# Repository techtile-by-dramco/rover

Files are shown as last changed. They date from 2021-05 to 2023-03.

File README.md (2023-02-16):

## Documentation

- The `rpi` folder contains the Python scripts to collect the sensor readings from the sensor-reader (`Sensorcombiner.py`) and driving the motors (with the rotary encoderers).
- The `scissor-lift` folder contains the files to talk the the scissor lift microcontrollers (Adruino Uno + custom-made shield) through Python. More information is included in the [docs](https://jarnevanmulders.github.io/scissor-lift-docs/).
- The `sensor-reader`folder contains the source files for the microcontroller to read-out all sensors on the rover. This microcontroller is read-out by the RPI on the rover (as dicussed above).

## System Architecture

Architecture

## System Description
To speed-up measurements, reduce labor-intensive tasks and mitigate human-errors, we have designed a rover
to perform automated 3D sampling inside the testbed. The rover consists of a baseplate, hosting the processing
unit and batteries, and a scissor lift to move the measurement equipment to the required height.

### Baseplate 
The baseplate contains a Raspberry Pi. A 16 cells battery pack, in a 4S4P configuration, powers the system. 
The battery voltage ranges from 10 V to 16.2 V depending on the charge state. The battery back, based on Lithium Cobalt Oxide (LCO) technology,
has a capacity of 170Wh and can handle up to 480W peak power. Besides powering the rover, the battery pack
provides power to the peripherals and measurement equipment in order to conduct the experiments. When
the battery is low, the rover is able to navigate to its charging station, recharge and resume the measurements.

### Navigation
Marvelmind indoor RTLS is used as a positioning system. It has a precision of 2 cm.
Ultrasonic beacons are used to acquire the position of the mobile beacon (mounted on the baseplate). Four
beacons are fixed in the Techtile infrastructure. The position is determined by trilateration. To filter out
outliers, we make use of a Kalman filter. The recursive algorithm uses consecutive inputs to estimate the
current state. Based on the uncertainties of the inputs and the uncertainties of the previous estimates, the
current state is approximated. Besides localization, the rover features obstacle detection to mitigate crashing into objects in the room. 
Ultrasonic sensors mounted on the sides of the rover’s baseplate are used and have
a resolution of 3 mm and a range of 2 cm to 400 cm.

### Scissor lift.
The baseplate of the rover can navigate through the room in 2D space. By mounting the scissor
lift on top of the baseplate, the rover is able to measure in 3D space. The lift has a range of 55 cm
to 185 cm. The equipment can be mounted on top of the lift. Power is supplied to the equipment from the
battery pack. The scissor lift can be controlled with AT-commands. The height of the lift is determined by
the VL53L1X Time-of-Flight (ToF) sensor using a 940 nm invisible Class 1 laser. An advertised accuracy and
ranging error of ± 20 mm in both ambient light and dark light conditions.

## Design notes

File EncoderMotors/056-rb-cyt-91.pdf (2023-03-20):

## RB-Cyt-91

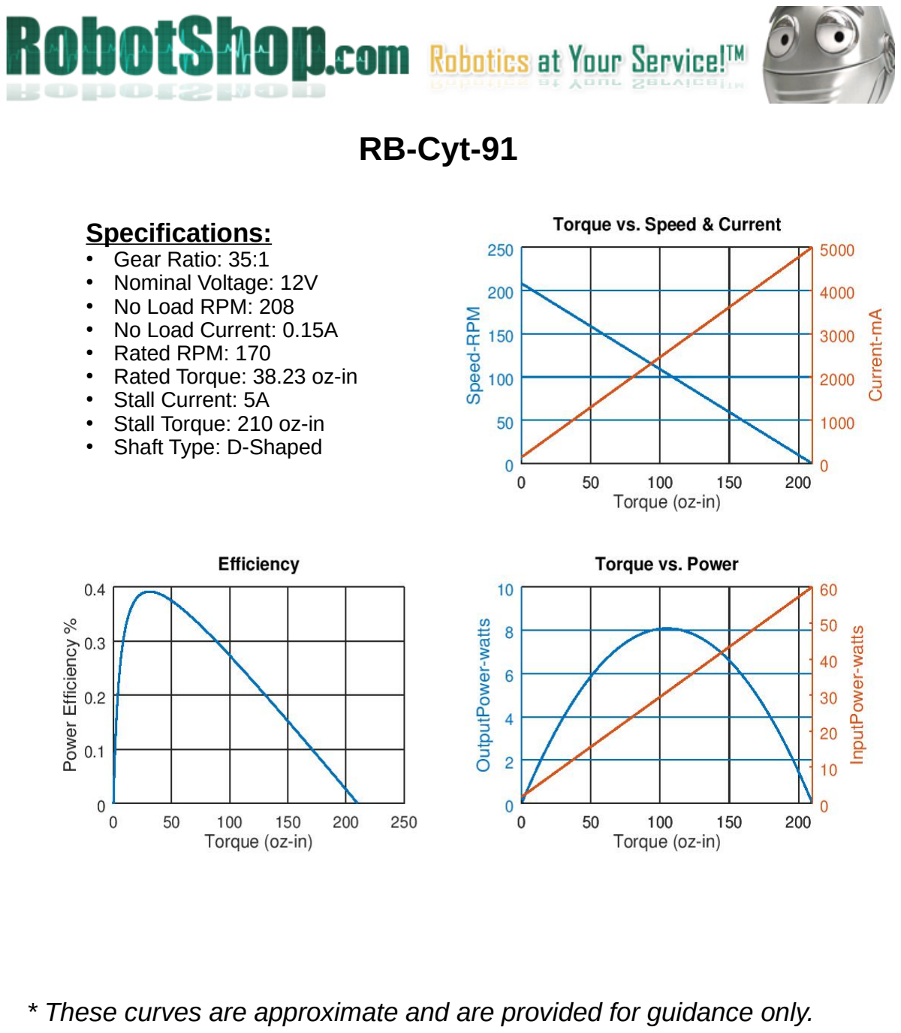
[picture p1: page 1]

* These curves are approximate and are provided for guidance only.

### Specifications:

- Gear Ratio: 35:1
- Nominal Voltage: 12V
- No Load RPM: 208
- No Load Current: 0.15A
- Rated RPM: 170
- Rated Torque: 38.23 oz-in
- Stall Current: 5A
- Stall Torque: 210 oz-in
- Shaft Type: D-Shaped

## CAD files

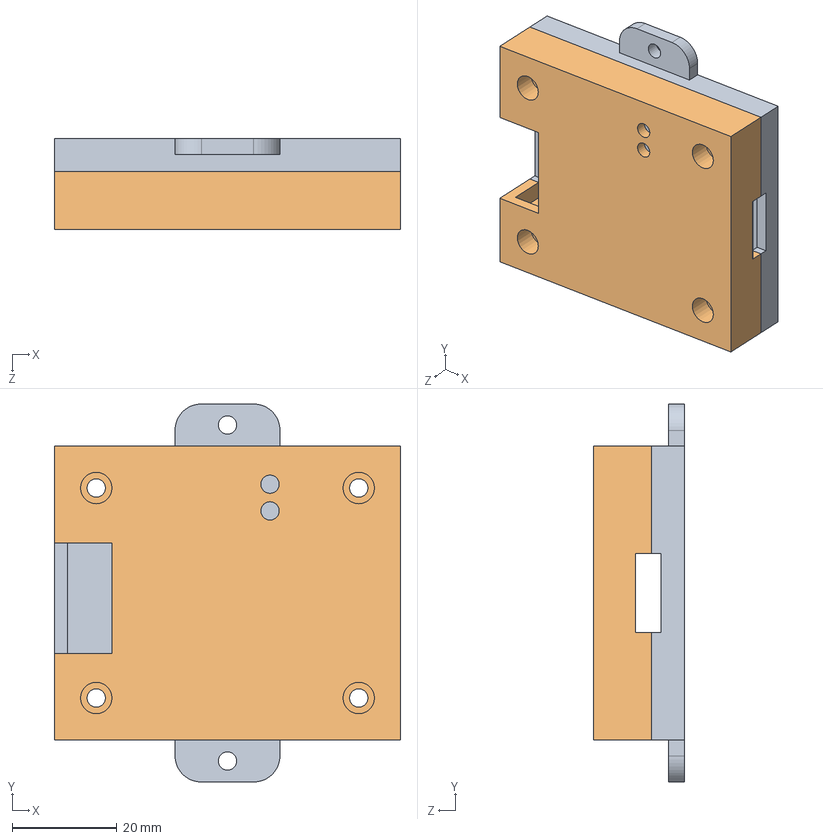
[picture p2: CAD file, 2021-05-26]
scissor-lift/drawings/Assembly/LEDstripControllerBox.SLDASM
66.0 x 72.0 x 17.3 mm
LEDstripController_Bottom
LEDstripController_Top

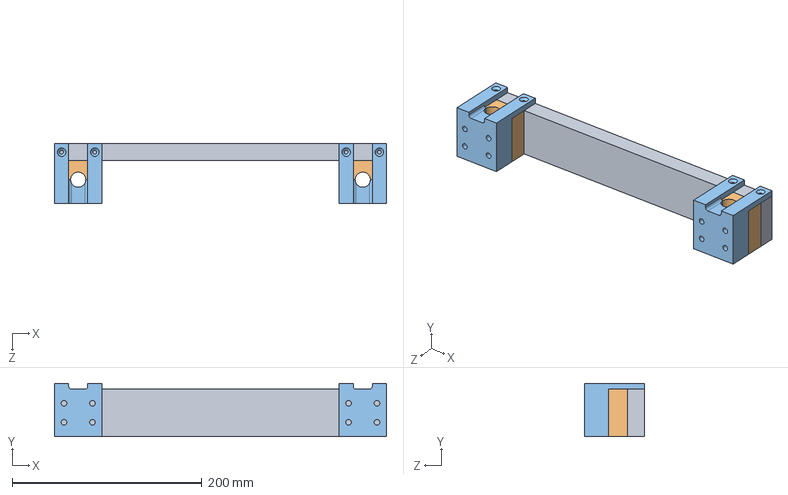
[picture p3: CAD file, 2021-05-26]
scissor-lift/drawings/Part-Files/Mounting_Fixed_Point_V2/Assembly_V2.SLDASM
350.0 x 56.0 x 63.0 mm
Scisser_Lift_Steel_Rod_Mounting_Part_Top_Fixed_Scissor_Wood
Scisser_Lift_Steel_Rod_Mounting_Part_Top_Fixed_Scissor x 2
Scisser_Lift_Steel_Rod_Mounting_Part x 2

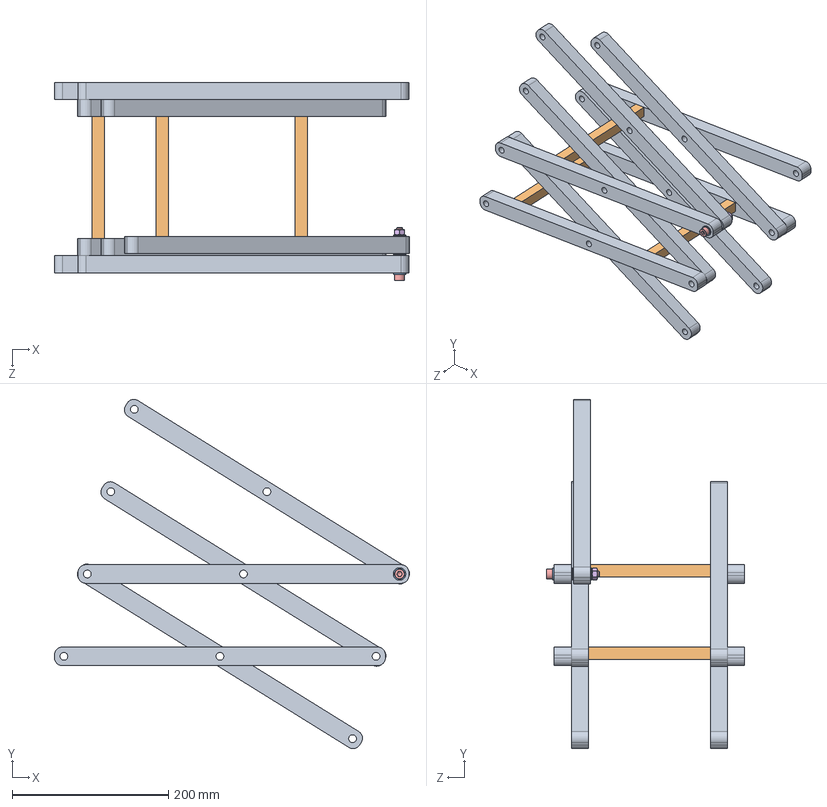
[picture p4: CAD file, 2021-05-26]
scissor-lift/drawings/Part-Files/Assembly.SLDASM
454.8 x 447.5 x 254.1 mm
Scisser_Lift_Main_Bar x 9
Scisser_Lift_Main_Bar_Transversal x 3
Scisser_Lift_Main_M8_Washer x 3
Scisser_Lift_Main_Round_Tube_23mm x 2
socket head cap screw_iso
hex nut style 1 gradeab_iso

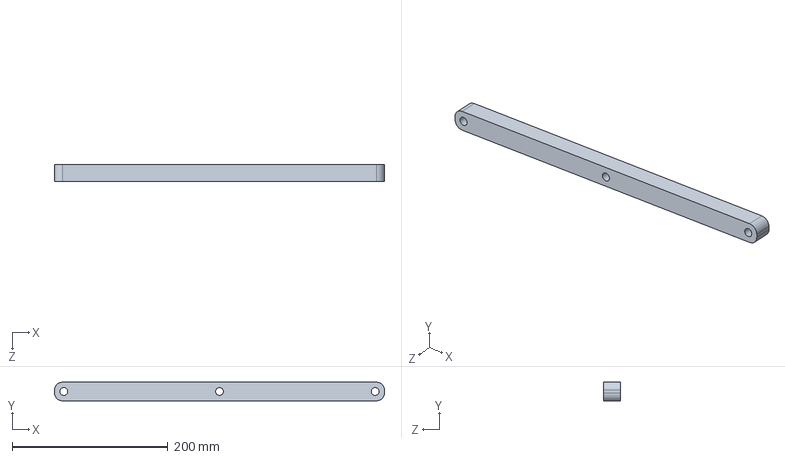
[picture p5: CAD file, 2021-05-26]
scissor-lift/drawings/Part-Files/Scisser_Lift_Main_Bar.SLDPRT
424.0 x 24.0 x 22.0 mm

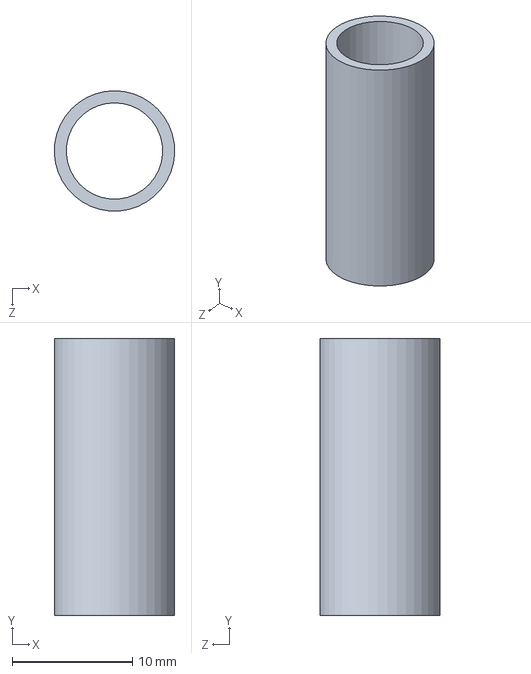
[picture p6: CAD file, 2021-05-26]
scissor-lift/drawings/Part-Files/Scisser_Lift_Main_Round_Tube_23mm.SLDPRT
9.99 x 23.0 x 10.0 mm

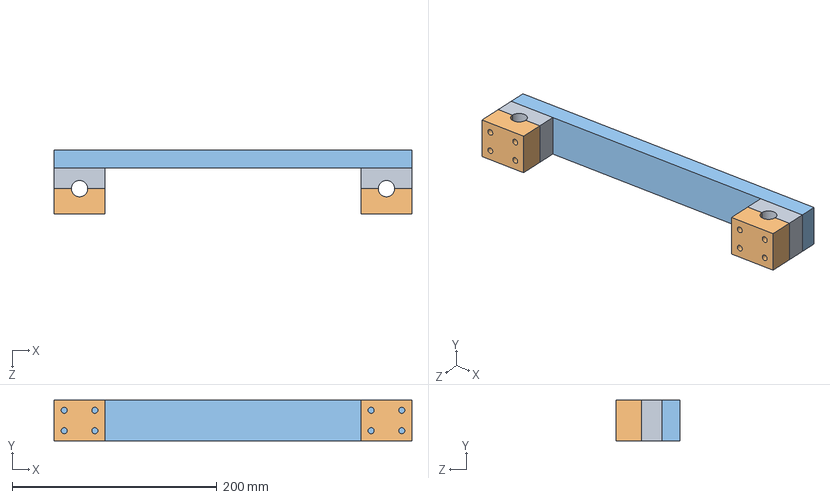
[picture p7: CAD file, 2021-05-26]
scissor-lift/drawings/Part-Files/Steel_Rod_Assembly_Fixed_Scissor.SLDASM
350.0 x 40.0 x 63.0 mm
Scisser_Lift_Steel_Rod_Mounting_Part_Top_Fixed_Scissor x 2
Scisser_Lift_Steel_Rod_Mounting_Part x 2
Scisser_Lift_Steel_Rod_Mounting_Part_Top_Fixed_Scissor_Wood

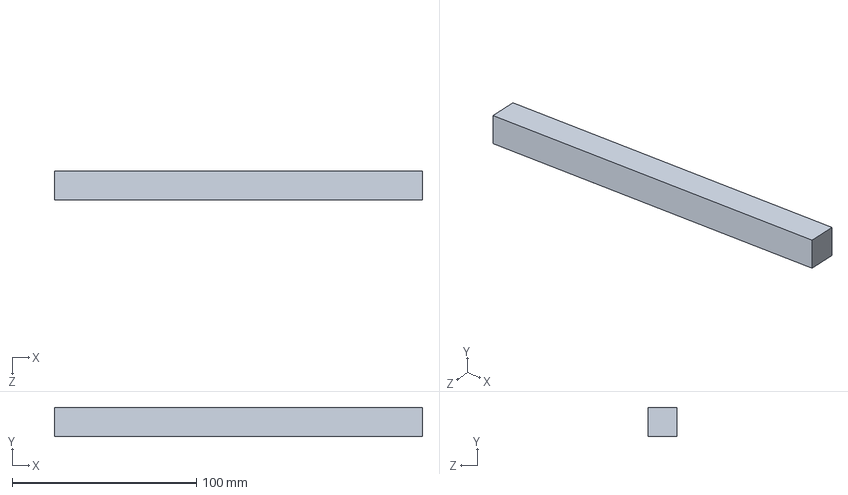
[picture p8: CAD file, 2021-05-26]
scissor-lift/drawings/Part-Files/Scisser_Lift_Main_Bar_Transversal.SLDPRT
200.0 x 16.0 x 16.0 mm

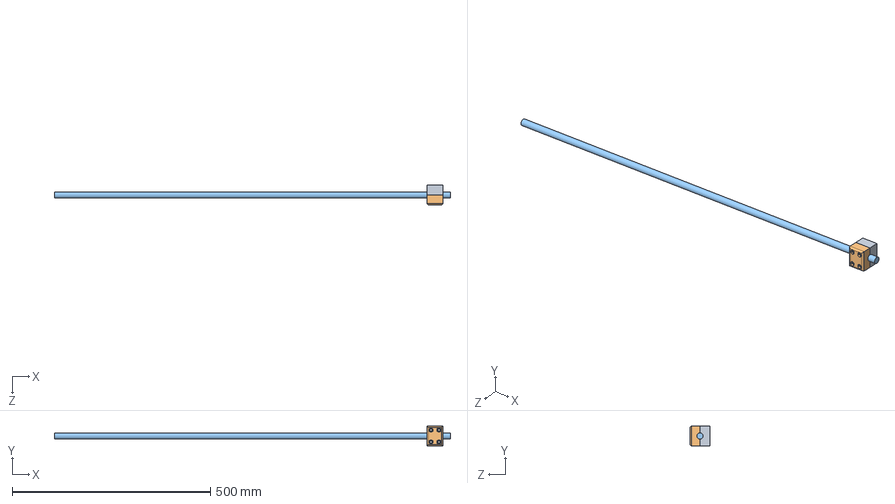
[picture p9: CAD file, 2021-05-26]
scissor-lift/drawings/Part-Files/Steel_Rod_Assembly.SLDASM
1000.0 x 50.0 x 50.0 mm
Scisser_Lift_Steel_Rod_Mounting_Part
Scisser_Lift_Steel_Rod_Mounting_Part_Top
Steel_Rod_16mm

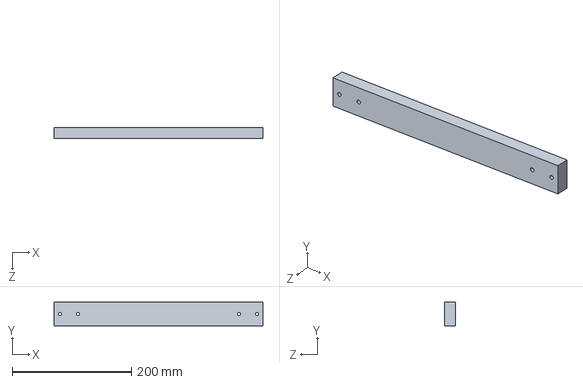
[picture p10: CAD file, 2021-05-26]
scissor-lift/drawings/Part-Files/Scisser_Lift_Steel_Rod_Mounting_Part_Top_Fixed_Scissor_Wood.SLDPRT
350.0 x 40.0 x 18.0 mm

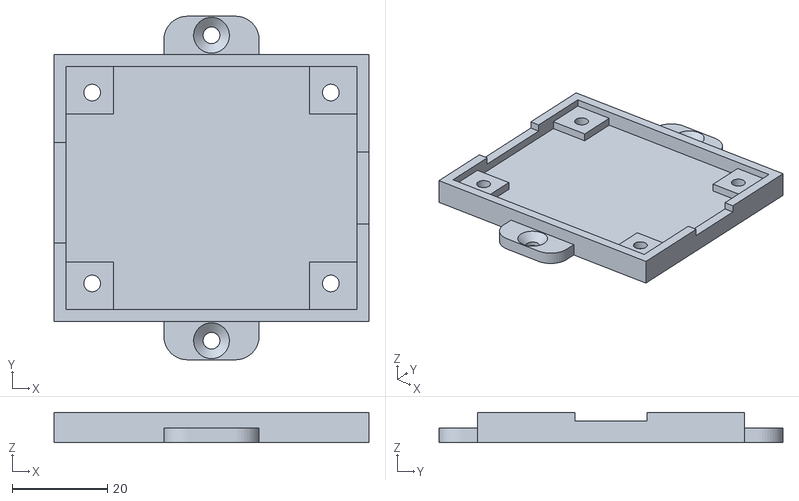
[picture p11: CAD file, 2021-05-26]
scissor-lift/drawings/STL-Files/LEDstripController_Bottom.STL
66.0 x 72.0 x 6.30

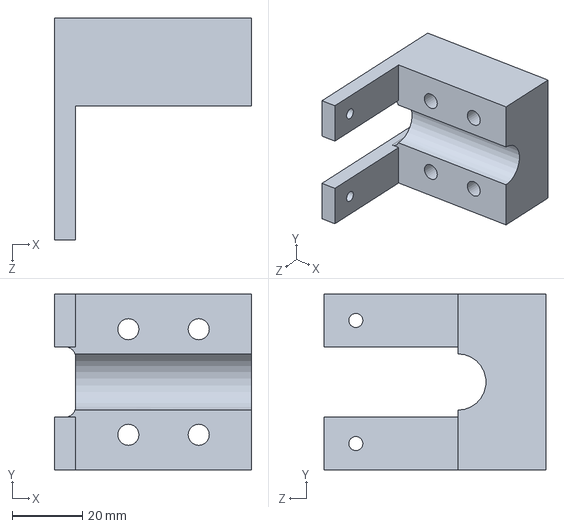
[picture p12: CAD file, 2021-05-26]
scissor-lift/drawings/Part-Files/Mounting_Fixed_Point_V2/Scisser_Lift_Steel_Rod_Mounting_Part.SLDPRT
56.0 x 50.0 x 63.0 mm

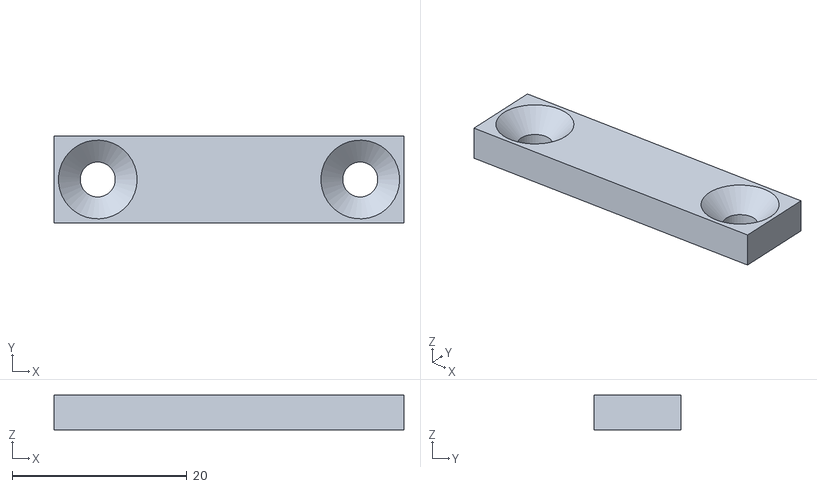
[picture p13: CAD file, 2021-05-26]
scissor-lift/drawings/STL-Files/LEDSTRIP_Mounting.STL
40.0 x 10.0 x 4.00

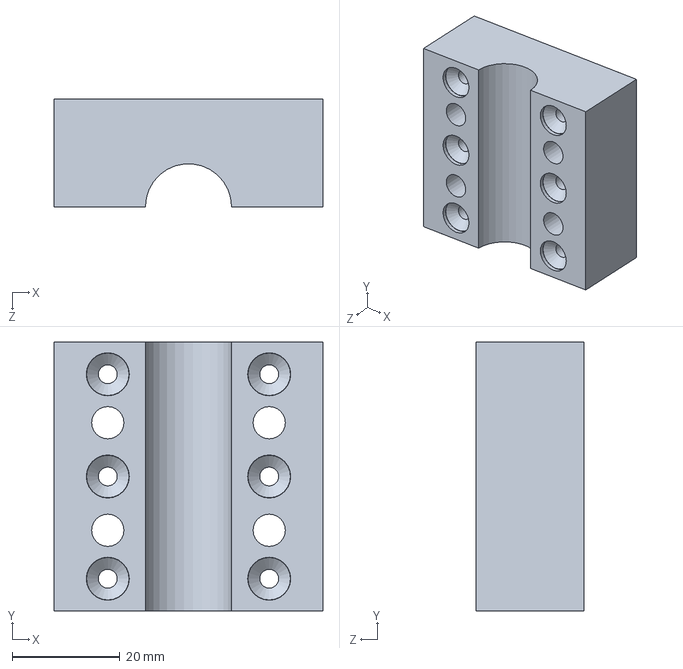
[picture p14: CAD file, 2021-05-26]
scissor-lift/drawings/Part-Files/Mounting_Fixed_Point_V2/Scisser_Lift_Steel_Rod_Mounting_Part_Top_Fixed_Scissor.SLDPRT
50.0 x 50.0 x 20.0 mm

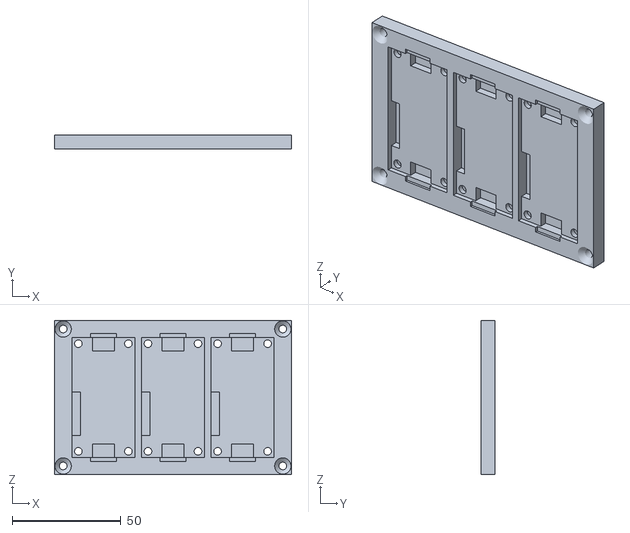
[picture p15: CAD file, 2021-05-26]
scissor-lift/drawings/STL-Files/Robot_MotorDriver.STL
109.0 x 6.50 x 71.0

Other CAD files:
scissor-lift/drawings/Part-Files/Mounting_Fixed_Point_V2/Scisser_Lift_Steel_Rod_Mounting_Part_Top_Fixed_Scissor_Wood.SLDPRT
scissor-lift/drawings/STL-Files/Mounting_External_FB_Converter.STL
scissor-lift/drawings/Part-Files/Scisser_Lift_Top_Plate_Bearing_Extention.SLDPRT
scissor-lift/drawings/STL-Files/Robot_Wheel_BearingPart.STL
scissor-lift/drawings/Drawing-Files/Robot_BottomPlate.SLDDRW
scissor-lift/drawings/Part-Files/SL_Top_Bearing_Parts/Washer_for_M5.SLDPRT
scissor-lift/drawings/Part-Files/SL_Top_Bearing_Parts/Washer_for_M5.STL
scissor-lift/drawings/Part-Files/SL_Top_Bearing_Parts/Washer_for_M5_Bearing.SLDPRT
scissor-lift/drawings/Part-Files/Scisser_Lift_Bevestiging_Schaar_Slider.SLDPRT
scissor-lift/drawings/Part-Files/Scisser_Lift_Bevestiging_Schaar_Slider_Fixed.SLDPRT
scissor-lift/drawings/Part-Files/Scisser_Lift_BoostConverterMounting.SLDPRT
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

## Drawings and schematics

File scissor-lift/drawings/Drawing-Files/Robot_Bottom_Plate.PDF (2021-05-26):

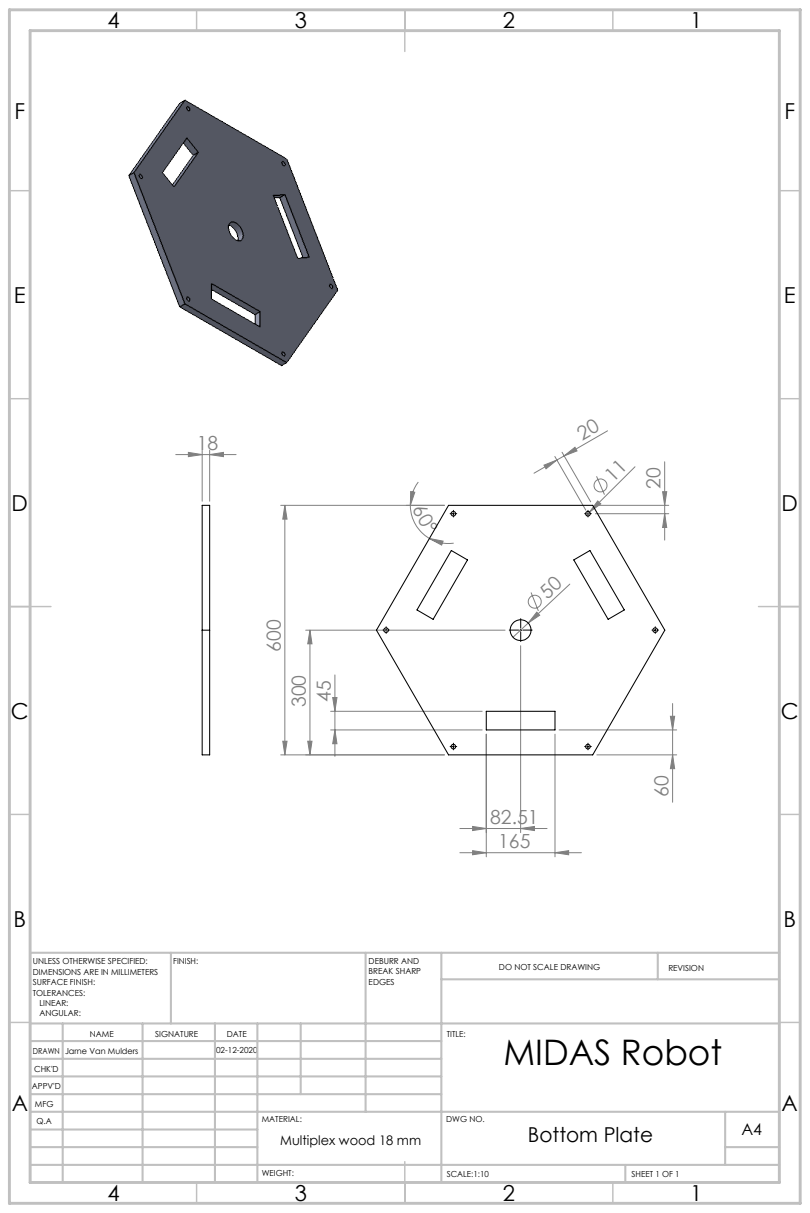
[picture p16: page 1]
FINISH:; DEBURR AND; BREAK SHARP; DO NOT SCALE DRAWING; REVISION; SCALE:1:10; SHEET 1 OF 1

UNLESS OTHERWISE SPECIFIED:
DIMENSIONS ARE IN MILLIMETERS
SURFACE FINISH:
TOLERANCES:
LINEAR:
ANGULAR:

NAME | SIGNATURE | DATE | | | | TITLE: MIDAS Robot

DRAWN | Jarne Van Mulders | | 02-12-2020
CHK'D
APPV'D
MFG
Q.A | | | | MATERIAL: | DWG NO. Bottom Plate | A4 Multiplex wood 18 mm

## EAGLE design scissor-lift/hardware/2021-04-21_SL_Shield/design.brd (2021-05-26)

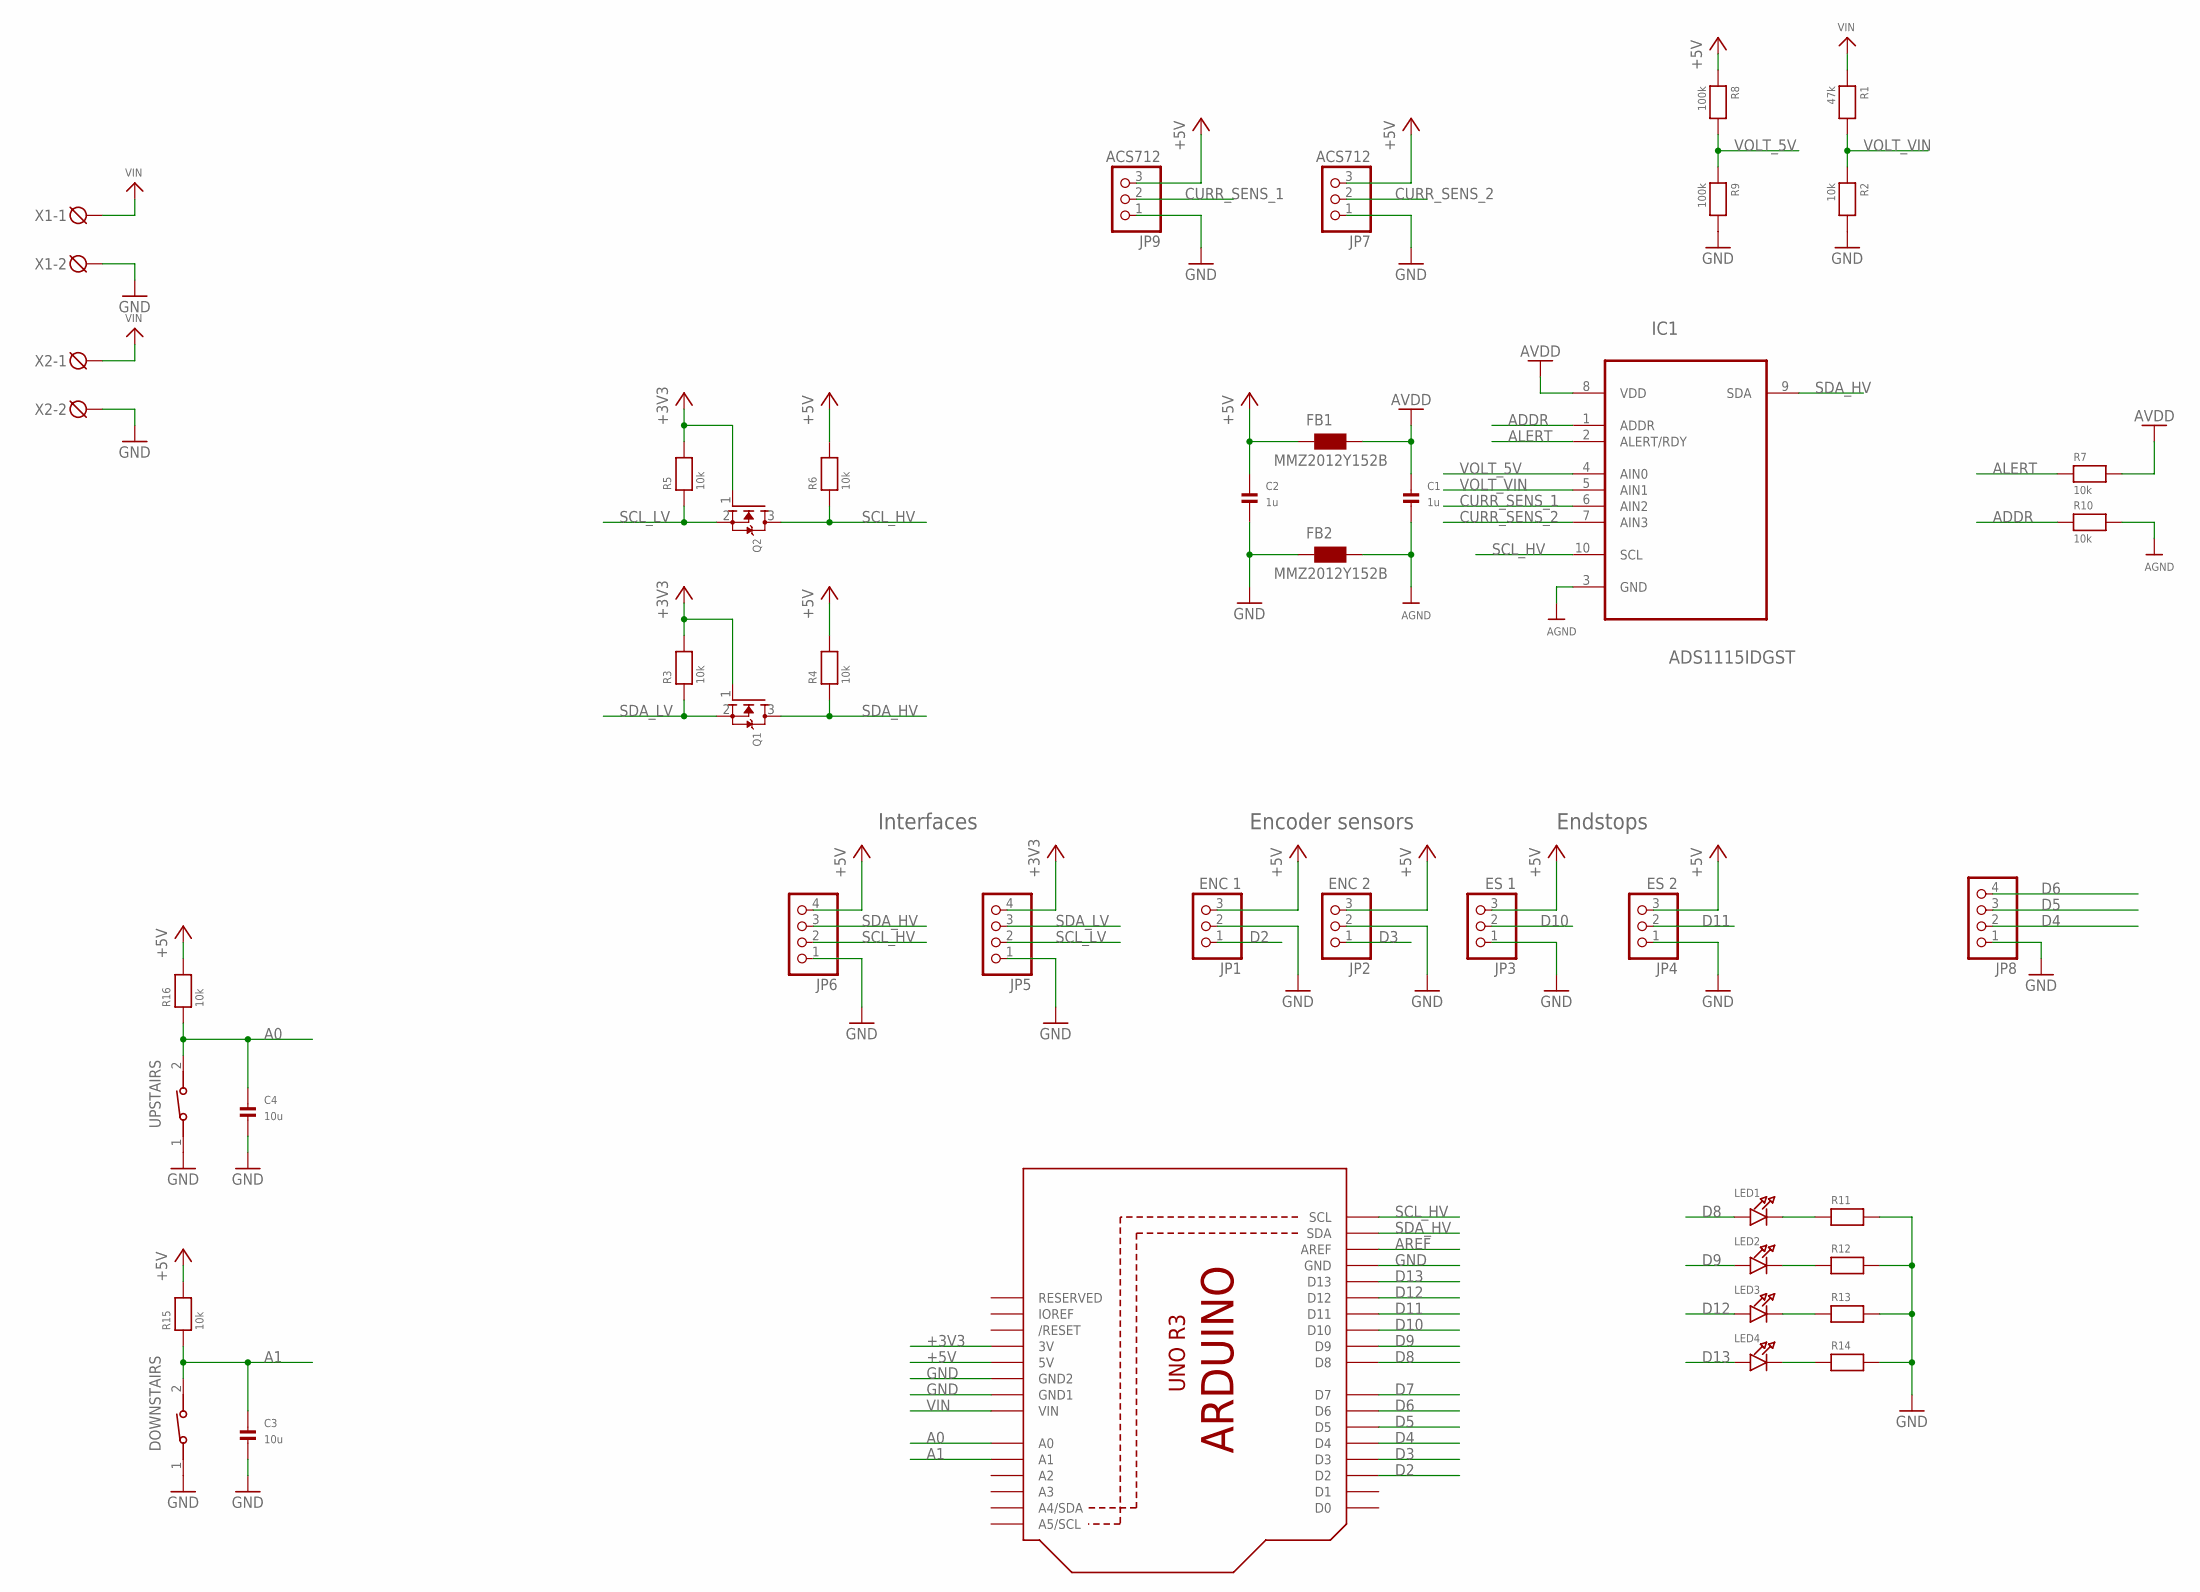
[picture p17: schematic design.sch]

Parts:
C1, C2: 1u; 0805
C3, C4: 10u; 0805
DOWNSTAIRS: 434111043826
FB1, FB2: MMZ2012Y152B; 0805
IC1: ADS1115IDGST; SOP50P490X110-10N
JP1: ENC 1; 1X03_ROUND
JP2: ENC 2; 1X03_ROUND
JP3: ES 1; 1X03_ROUND
JP4: ES 2; 1X03_ROUND
JP5, JP6, JP8: HEADER-1X4ROUND; 1X04_ROUND
JP7, JP9: ACS712; 1X03_ROUND
LED1, LED2, LED3, LED4: LED0805; CHIPLED_0805
Q1, Q2: MOSFET-NWIDE; SOT23-WIDE
R1: 47k; 0603
R2, R3, R4, R5, R6, R7, R10, R15, R16: 10k; 0603
R8, R9: 100k; 0603
R11, R12, R13, R14: RESISTOR0603; 0603
U1: ARDUINOR3NODIM; ARDUINOR3-NODIM
UPSTAIRS: 434111043826
X1, X2: DG3XX-02-5.0; DG306-5.0-02P

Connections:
+3V3: JP5.4, Q1.1 (G), Q2.1 (G), R3.2, R5.2, U1.3V
+5V: C2.1, FB1.1, JP1.3, JP2.3, JP3.3, JP4.3, JP6.4, JP7.3, JP9.3, R4.2, R6.2, R8.1, R15.2, R16.2, U1.5V
A0: C4.1, R16.1, U1.A0, UPSTAIRS.2
A1: C3.1, DOWNSTAIRS.2, R15.1, U1.A1
ADDR: IC1.1 (ADDR), R10.1
AGND: C1.2, FB2.2, IC1.3 (GND), R10.2
ALERT: IC1.2 (ALERT/RDY), R7.1
AREF: U1.AREF
AVDD: C1.1, FB1.2, IC1.8 (VDD), R7.2
CURR_SENS_1: IC1.6 (AIN2), JP9.2
CURR_SENS_2: IC1.7 (AIN3), JP7.2
D2: JP1.1, U1.D2
D3: JP2.1, U1.D3
D4: JP8.2, U1.D4
D5: JP8.3, U1.D5
D6: JP8.4, U1.D6
D7: U1.D7
D8: LED1.A, U1.D8
D9: LED2.A, U1.D9
D10: JP3.2, U1.D10
D11: JP4.2, U1.D11
D12: LED3.A, U1.D12
D13: LED4.A, U1.D13
GND: C2.2, C3.2, C4.2, DOWNSTAIRS.1, FB2.1, JP1.2, JP2.2, JP3.1, JP4.1, JP5.1, JP6.1, JP7.1, JP8.1, JP9.1, R2.2, R9.2, R11.2, R12.2, R13.2, R14.2, U1.GND, U1.GND1, U1.GND2, UPSTAIRS.1, X1.2, X2.2
unnamed: LED1.C, R11.1
unnamed: LED2.C, R12.1
unnamed: LED3.C, R13.1
unnamed: LED4.C, R14.1
SCL_HV: IC1.10 (SCL), JP6.2, Q2.3 (D), R6.1, U1.SCL
SCL_LV: JP5.2, Q2.2 (S), R5.1
SDA_HV: IC1.9 (SDA), JP6.3, Q1.3 (D), R4.1, U1.SDA
SDA_LV: JP5.3, Q1.2 (S), R3.1
VIN: R1.1, U1.VIN, X1.1, X2.1
VOLT_5V: IC1.4 (AIN0), R8.2, R9.1
VOLT_VIN: IC1.5 (AIN1), R1.2, R2.1

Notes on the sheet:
Encoder sensors
Endstops
Interfaces

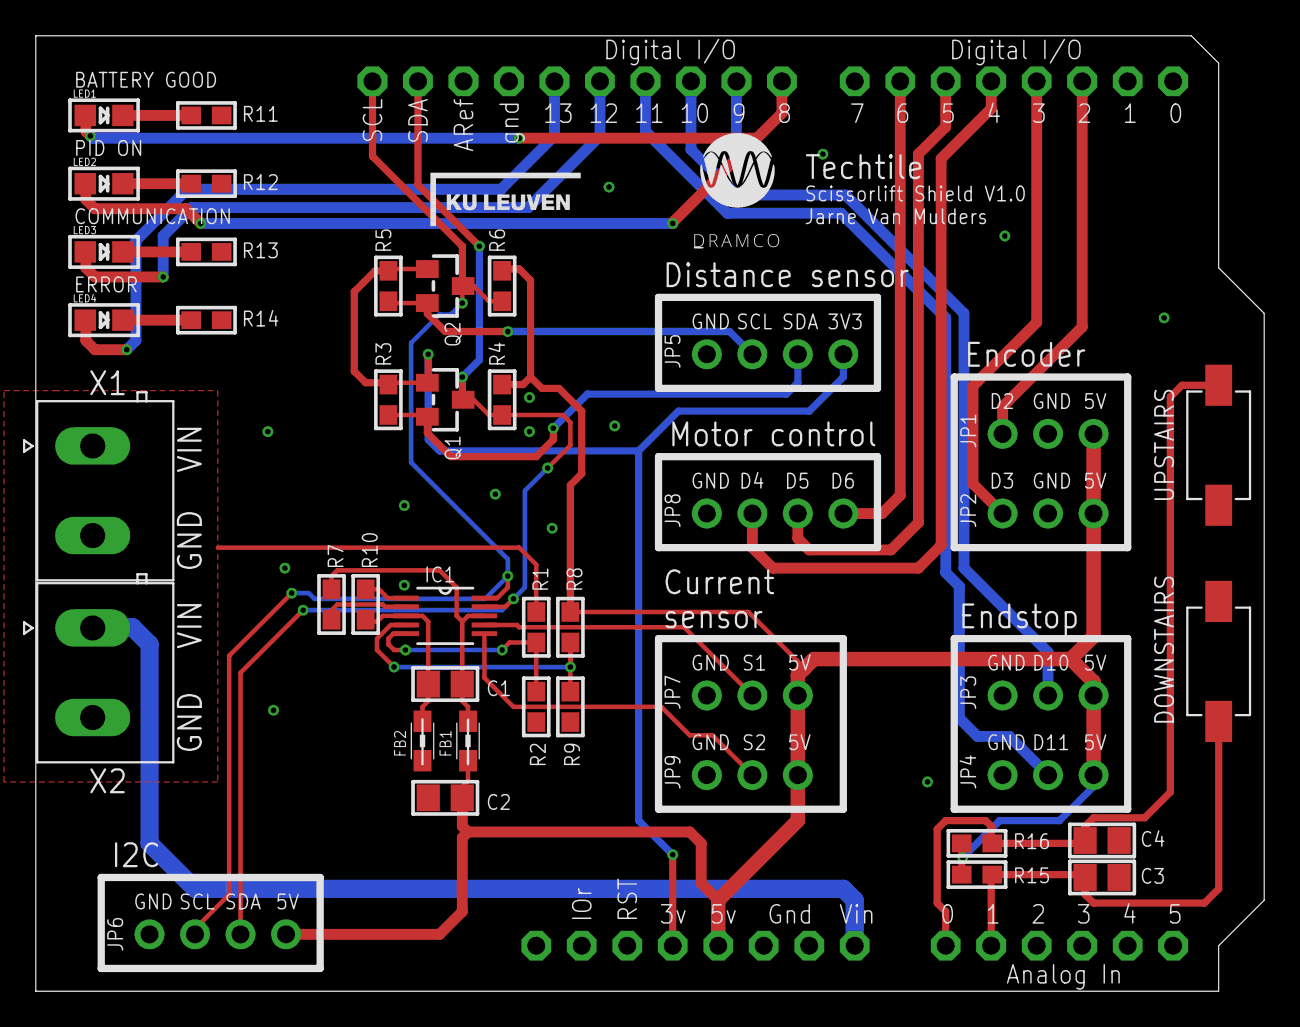
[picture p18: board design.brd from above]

Board: 2 copper layers, 68.6 x 53.3 mm, 43 parts (0 on the bottom side), 33 nets.

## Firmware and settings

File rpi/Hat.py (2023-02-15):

#!/usr/bin/env python

# from subprocess import HIGH_PRIORITY_CLASS
# from syslog import LOG_WARNING
from smbus import SMBus
import time
import RPi.GPIO as IO

i2cbus = 0

#===========================================
#===       ***  I2C ADRESSES ***         ===
#===========================================

I2C_IOEXP_1 = 0x20
I2C_IOEXP_2 = 0x21

#===========================================
#===         ***  Registers ***          ===
#===========================================

IODIRA      = 0x00  # IO direction A - 1= input 0 = output
IODIRB      = 0x01  # IO direction B - 1= input 0 = output    
IPOLA       = 0x02  # Input polarity A
IPOLB       = 0x03  # Input polarity B
GPINTENA    = 0x04  # Interrupt-onchange A
GPINTENB    = 0x05  # Interrupt-onchange B
DEFVALA     = 0x06  # Default value for port A
DEFVALB     = 0x07  # Default value for port B
INTCONA     = 0x08  # Interrupt control register for port A
INTCONB     = 0x09  # Interrupt control register for port B
IOCON       = 0x0A  # Configuration register
GPPUA       = 0x0C  # Pull-up resistors for port A
GPPUB       = 0x0D  # Pull-up resistors for port B
INTFA       = 0x0E  # Interrupt condition for port A
INTFB       = 0x0F  # Interrupt condition for port B
INTCAPA     = 0x10  # Interrupt capture for port A
INTCAPB     = 0x11  # Interrupt capture for port B
GPIOA       = 0x12  # Data port A
GPIOB       = 0x13  # Data port B
OLATA       = 0x14  # Output latches A
OLATB       = 0x15  # Output latches B

#===========================================
#===      ***  Status Integers ***       ===
#===========================================


#===========================================
#===       ***  Cross Define ***         ===
#===========================================

# I2C_IOEXP_2 -- PORT A -- PINS

MOTOR_1_CTRL_INA    =   0
MOTOR_1_CTRL_INB    =   1

MOTOR_2_CTRL_INA    =   2
MOTOR_2_CTRL_INB    =   3

MOTOR_3_CTRL_INA    =   4
MOTOR_3_CTRL_INB    =   5

# I2C_IOEXP_2 -- PORT B -- PINS

MOTOR_1_EN          =   0
MOTOR_2_EN          =   1
MOTOR_3_EN          =   2

# MOTORS
MOTOR_1             =   1
MOTOR_2             =   2
MOTOR_3             =   3

# VALUE
LOW                 =   0
HIGH                =   1

# PWM
PWM_FREQ            =   1000

MOTOR_1_PWM         =   13
MOTOR_2_PWM         =   19
MOTOR_3_PWM         =   26



class Hat():

    def __init__(self):
        self.i2cbus = SMBus(1)

        self.status = [0,0,0,0]

        self.i2cbus.write_byte_data(I2C_IOEXP_1, IOCON, 0x02)   # Update configuration register
        
        
        self.i2cbus.write_byte_data(I2C_IOEXP_2, IOCON, 0x02)   # Update configuration register
        
        self.i2cbus.write_byte_data(I2C_IOEXP_2, IODIRA, 0x00)  # Set Port A as outputs
        self.i2cbus.write_byte_data(I2C_IOEXP_2, IODIRB, 0x00)  # Set Port B as outputs


        IO.setwarnings(False)                       #   Do not show warnings
        IO.setmode(IO.BCM)                          #   Programming the GPIO by BCM pin numbers
        IO.setup(MOTOR_1_PWM, IO.OUT)               #   Initialize GPIO13 as an output.
        IO.setup(MOTOR_2_PWM, IO.OUT)               #   Initialize GPIO19 as an output.
        IO.setup(MOTOR_3_PWM, IO.OUT)               #   Initialize GPIO26 as an output.

        self.p1 = IO.PWM(MOTOR_1_PWM, PWM_FREQ)
        self.p2 = IO.PWM(MOTOR_2_PWM, PWM_FREQ)
        self.p3 = IO.PWM(MOTOR_3_PWM, PWM_FREQ)

        self.p1.start(0)
        self.p2.start(0)
        self.p3.start(0)

    #===========================================
    #===        ***  IO Expander ***         ===
    #===========================================    

    def set_status_reg(self, i2c, port, status_nr, bit_number, value):

        if value:
            self.status[status_nr] = self.status[status_nr] | (1 << bit_number)
        else:
            self.status[status_nr] = self.status[status_nr] & ~(1 << bit_number)

        self.i2cbus.write_byte_data(i2c, port, self.status[status_nr])
    
    
    def set_bit_port(self, i2c, port, bit_number, value):

        if i2c == I2C_IOEXP_1 and port == GPIOA:
            self.set_status_reg(I2C_IOEXP_1, GPIOA, 0, bit_number, value)

        if i2c == I2C_IOEXP_1 and port == GPIOB:
            self.set_status_reg(I2C_IOEXP_1, GPIOB, 1, bit_number, value)

        if i2c == I2C_IOEXP_2 and port == GPIOA:
            self.set_status_reg(I2C_IOEXP_2, GPIOA, 2, bit_number, value)

        if i2c == I2C_IOEXP_2 and port == GPIOB:
            self.set_status_reg(I2C_IOEXP_2, GPIOB, 3, bit_number, value)

    
    def set_bit_io2_porta(self, bit_number, value):
        self.set_bit_port(I2C_IOEXP_2, GPIOA, bit_number, value)

    def set_bit_io2_portb(self, bit_number, value):
        self.set_bit_port(I2C_IOEXP_2, GPIOB, bit_number, value)


    #===========================================
    #===         ***  Functions ***          ===
    #===========================================

    #   Motor change direction

    def set_dir(self, dir, pin1, pin2):
        if dir:
            self.set_bit_io2_porta(pin1, HIGH)
            self.set_bit_io2_porta(pin2, LOW)
        else:
            self.set_bit_io2_porta(pin1, LOW)
            self.set_bit_io2_porta(pin2, HIGH)


    def set_dir_motor(self, motor, dir):
        if motor == MOTOR_1:
            self.set_dir(dir, MOTOR_1_CTRL_INA, MOTOR_1_CTRL_INB)
        if motor == MOTOR_2:
            self.set_dir(dir, MOTOR_2_CTRL_INA, MOTOR_2_CTRL_INB)
        if motor == MOTOR_3:
            self.set_dir(dir, MOTOR_3_CTRL_INA, MOTOR_3_CTRL_INB)

    
    #   Motor enable/disable

    def enable_motor(self, motor):
        if motor == MOTOR_1:
            self.set_bit_io2_portb(MOTOR_1_EN, HIGH)
        if motor == MOTOR_2:
            self.set_bit_io2_portb(MOTOR_2_EN, HIGH)
        if motor == MOTOR_3:
            self.set_bit_io2_portb(MOTOR_3_EN, HIGH)

    def disable_motor(self, motor):
        if motor == MOTOR_1:
            self.set_bit_io2_portb(MOTOR_1_EN, LOW)
        if motor == MOTOR_2:
            self.set_bit_io2_portb(MOTOR_2_EN, LOW)
        if motor == MOTOR_3:
            self.set_bit_io2_portb(MOTOR_3_EN, LOW)
    
    def enable_all_motors(self):
        self.enable_motor(MOTOR_1)
        self.enable_motor(MOTOR_2)
        self.enable_motor(MOTOR_3)

    def disable_all_motors(self):
        self.disable_motor(MOTOR_1)
        self.disable_motor(MOTOR_2)
        self.disable_motor(MOTOR_3)
    
    def set_speed_motor(self, motor, speed):
        if motor == MOTOR_1:
            self.p1.start(speed)
        if motor == MOTOR_2:
            self.p2.start(speed)
        if motor == MOTOR_3:
            self.p3.start(speed)




#     def main():
#         '''
#         Main program function
#         '''

#         i2cbus = SMBus(1)  # Create a new I2C bus
#         i2caddress = 0x21  # Address of MCP23017 device

#         i2cbus.write_byte_data(i2caddress, IOCON, 0x02)  # Update configuration register

#         i2cbus.write_byte_data(i2caddress, IODIRA, 0x00)  # Set Port A as outputs and Port B as inputs
#         i2cbus.write_byte_data(i2caddress, IODIRB, 0xFF)  # Set Port A as outputs and Port B as inputs

#         while (True):
#             porta = i2cbus.read_byte_data(i2caddress, GPIOA)  # Read the value of Port B
#             print(porta.to_bytes(1, 'big')) # print the value of Port B
            
#             portb = i2cbus.read_byte_data(i2caddress, GPIOB)  # Read the value of Port B
#             print(portb.to_bytes(1, 'big')) # print the value of Port B

#             a = i2cbus.read_byte_data(i2caddress, IODIRA)
#             print('IODIRA ' + str(a))
#             a = i2cbus.read_byte_data(i2caddress, IODIRB)
#             print('IODIRB ' + str(a))

#             if porta == 0x00:
#                 i2cbus.write_byte_data(i2caddress, GPIOA, 0x88)  # Set pin 1 to on
#             else:
#                 i2cbus.write_byte_data(i2caddress, GPIOA, 0x00)  # Set pin 1 to on
#             time.sleep(1)  # Wait 500ms

#             # i2cbus.write_byte_data(i2caddress, GPIOA, 0x00)  # Set pin 1 to off
#             # time.sleep(0.5)  # Wait 500ms


# if __name__ == "__main__":
#     main()

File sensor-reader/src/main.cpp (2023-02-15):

#include <Arduino.h>
#include "Config.h"
#include "MsgHandler.h"
#include "SensorDriver.h"

//#define DEBUG

SensorDriver sensor_driver;
MsgHandler com_handler(&sensor_driver);

bool execute_enable;

void setup() {

  #ifdef DEBUG
    SerialUSB.begin(115200);
  #endif

  sensor_driver.init();

  SER.begin(2000000);

}


void loop() {

  com_handler.rx_msg_handler();

  com_handler.run();


}

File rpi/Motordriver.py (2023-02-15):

from Hat import Hat
from Encoder import Encoder
import time
from simple_pid import PID
from time import sleep, perf_counter
from threading import Thread


prev = time.time()


class Motordriver():

      def __init__(self, hat, ec):
            self.hat = hat
            self.ec = ec

            self.speed = [30, 0, 0]

            self._running = False
            self.speedchanged = False

            self.pid_buffer = [PID(0.2, 1.5, 0.01), PID(0.2, 1.5, 0.01), PID(0.2, 1.5, 0.01)]
            self.pid_controller_enable = [False, False, False]
            self.duty_cycle = [0, 0, 0]

            t1 = Thread(target=self.task)
            t1.start()

            
      def print_rpm(self):
            print("Rotates Per Minute Update")
            print("Motor 1 RPM: " + str(self.ec.get_rpm(0)))
            print("Motor 2 RPM: " + str(self.ec.get_rpm(1)))
            print("Motor 3 RPM: " + str(self.ec.get_rpm(2)))


      # THREAD
      def task(self):
            while 1:
                  time.sleep(0.1)
                  for i in range(3):
                        self.duty_cycle[i] = self.pid_buffer[i](self.ec.get_rpm(i))
                        
                        if self.pid_controller_enable[i] and self.duty_cycle[i] < 100 and self.duty_cycle[i] > 0:
                              self.hat.set_speed_motor(i + 1, self.duty_cycle[i])
                  
                  #self.print_motor_updates()


      def print_motor_updates(self):      
            global prev            
            if time.time() - prev > 1:
                  prev = time.time()
                  print("Update motors")
                  for i in range(3):
                        print('Duty Cycle: ' + str(self.duty_cycle[i]) + ' -- RPM: ' + str(self.ec.get_rpm(i)))

      def update_speed(self, motor, rpm):
            self.pid_buffer[motor].setpoint = rpm
            if rpm == 0:
                  self.pid_buffer[motor].auto_mode = False
                  self.pid_buffer[motor] = PID(0.2, 1.5, 0.01)
                  self.pid_controller_enable[motor] = False
                  self.hat.set_speed_motor(motor + 1, 0)
            else:
                  self.pid_buffer[motor].auto_mode = True
                  self.pid_controller_enable[motor] = True
















      # # def task1(self):
  
      # #       pid = PID(0.2, 1.5, 0.2, setpoint=self.speed[0])
      # #       while 1:

      # #             if self.speedchanged:
      # #                   self.speedchanged = False
      # #                   a = self.ec.get_rpm(0)
      # #                   pid = PID(0.2, 1.5, 0.2, setpoint=self.speed[0])
      # #                   self.hat.set_speed_motor(1, a)

      # #             if self._running:

      # #                   control = pid(self.ec.get_rpm(0))
                        
      # #                   if control < 100 and control > 0:
      # #                         self.hat.set_speed_motor(1, control)
      # #                   if control > 100:
      # #                         self.hat.set_speed_motor(1, 100)
      # #                   if control < 0:
      # #                         self.hat.set_speed_motor(1, 0)

      # #                   global prev
                        
      # #                   if time.time() - prev > 1:
      # #                         prev = time.time()
      # #                         print(control)
      # #                         print('RPM ' + str(self.ec.get_rpm(0)))

      # #             else:
      # #                   self.hat.set_speed_motor(1, 0)
      # #                   pid = PID(0.2, 1.5, 0.2, setpoint=self.speed[0])


      # # def task2(self):
  
      # #       pid = PID(0.2, 1.5, 0.2, setpoint=self.speed[1])
      # #       while 1:

      # #             if self.speedchanged:
      # #                   self.speedchanged = False
      # #                   a = self.ec.get_rpm(0)
      # #                   pid = PID(0.2, 1.5, 0.2, setpoint=self.speed[1])
      # #                   self.hat.set_speed_motor(1, a)

      # #             if self._running:

      # #                   control = pid(self.ec.get_rpm(0))
                        
      # #                   if control < 100 and control > 0:
      # #                         self.hat.set_speed_motor(2, control)
      # #                   if control > 100:
      # #                         self.hat.set_speed_motor(2, 100)
      # #                   if control < 0:
      # #                         self.hat.set_speed_motor(2, 0)

      # #                   global prev
                        
      # #                   if time.time() - prev > 1:
      # #                         prev = time.time()
      # #                         print(control)
      # #                         print('RPM ' + str(self.ec.get_rpm(1)))

      # #             else:
      # #                   self.hat.set_speed_motor(2, 0)
      # #                   pid = PID(0.2, 1.5, 0.2, setpoint=self.speed[1])

      # # def task3(self):
  
      # #       pid = PID(0.2, 1.5, 0.2, setpoint=self.speed[0])
      # #       while 1:

      # #             if self.speedchanged:
      # #                   self.speedchanged = False
      # #                   a = self.ec.get_rpm(0)
      # #                   pid = PID(0.2, 1.5, 0.2, setpoint=self.speed[0])
      # #                   self.hat.set_speed_motor(1, a)

      # #             if self._running:

      # #                   control = pid(self.ec.get_rpm(0))
                        
      # #                   if control < 100 and control > 0:
      # #                         self.hat.set_speed_motor(1, control)
      # #                   if control > 100:
      # #                         self.hat.set_speed_motor(1, 100)
      # #                   if control < 0:
      # #                         self.hat.set_speed_motor(1, 0)

      # #                   global prev
                        
      # #                   if time.time() - prev > 1:
      # #                         prev = time.time()
      # #                         print(control)
      # #                         print('RPM ' + str(self.ec.get_rpm(0)))

      # #             else:
      # #                   self.hat.set_speed_motor(1, 0)
      # #                   pid = PID(0.2, 1.5, 0.2, setpoint=self.speed[0])








      
      # # def set_speed_rpm(self, rpm):
      # #       self.speedchanged = True
      # #       self.speed[1] = rpm

      # def start(self):
      #       self._running = True

      # def stop(self):
      #       self._running = False

      # def set_speed_rpm(self, rpm):     
      #       # print('ok-1')

      #       pid = PID(0.2, 1.5, 0.01, setpoint=rpm)

      #       # print('ok0')

      #       # t1 = Thread(target=task_pid1(self, pid))

            
      #       # #self.hat.set_speed_motor(1, 40)

      #       # print('ok')

      #       # t1.start()

      #       # print('ok2')
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

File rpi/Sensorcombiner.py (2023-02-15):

import time
from threading import Thread

BEGIN_DELIMITER             = b'\x02'    #  Test connection

#===========================================
#===          ***  Requests ***          ===
#===========================================

TEST_CONNECTION             = b'\x01'    #  Test connection

#   Set Commands

SET_UPDATE_RATE             = b'\x10'    #  Set Update Rate
SET_RANGE                   = b'\x11'    #  Set maximum range, values above are ignored
SET_START_SCANNING          = b'\x12'    #  Start scanning
SET_STOP_SCANNING           = b'\x13'    #  Stop scanning
SET_OBJECT_DETECTION_RANGE  = b'\x15'    #  Minimum range before alert message is generated
SET_SCANNING_FREQ           = b'\x16'    #  Change scanning rate

SET_ALERT_RANGE             = b'\x20'   #  Set ALERT range
SET_ALERT_ENABLE            = b'\x21'   #  Enable alert message
SET_ALERT_DISABLE           = b'\x22'   #  Disable alert message

#   Get commands
GET_POSITIONS_ALL           = b'\x30'   #  Return all 12 positions
GET_POSITION_FROM_NR        = b'\x31'   #  Return position from given number

#===========================================
#===       ***  Confirmations ***        ===
#===========================================

RX_MSG_CMF                  = b'\xA0'   #  Confirmation command received (checksum comfirmed)

#===========================================
#===        ***  Indications ***         ===
#===========================================

ALERT_IND                   = b'\x40'   #  Alert indication
AUTO_POS_IND                = b'\x41'   #  If scanning enable, send positions over SERIAL bus

#===========================================
#===        ***  Responses ***           ===
#===========================================

POSITIONS_ALL_RSP           = b'\x50'   #  Return all positions



class Sensorcombiner():

    def __init__(self, port):
        self.port = port

        t1 = Thread(target=self.task)
        t1.start()

        self.distancebuffer = [0,0,0,0,0,0,0,0,0,0,0,0]

    def test_connection(self):
        self.send_message_no_data(TEST_CONNECTION)
        return self.read_respons()

    def start_scanning(self):
        # self.port.write(b'\x02\x12\x00')
        self.send_message_no_data(SET_START_SCANNING)

    def stop_scanning(self):
        # self.port.write(b'\x02\x13\x00')
        self.send_message_no_data(SET_STOP_SCANNING)
    
    def change_update_rate(self, rate):
        self.send_message_data(SET_SCANNING_FREQ, rate)

    def get_positions(self):
        self.send_message_no_data(GET_POSITIONS_ALL)



#===        ***  Communication Functions ***           ===

    #   Readings

    def read_convert_result(self):
        result = 0 
        response = 0
        time.sleep(0.001)
        while self.port.in_waiting > 0:
            if self.port.read(1) == b'\x02':
                res = self.port.read(2)
                response = res [0]
                num = int.from_bytes(res[1:2], "big")
                #print("num is:" + str(num))
                if(num != 0):
                    ab = self.port.read(num)
                    result = ab[0] | (ab[1] << 8) | (ab[2] << 16) | (ab[3] << 24)
                    break
        return result, response


    def read_respons(self):
        result = 0
        response = 0
        res = 0
        dat_buf = 0
        num = 0
        while self.port.in_waiting > 0:
            #aa = self.port.read(1)
            #print('init read: ' + str(aa))
            if self.port.read(1) == BEGIN_DELIMITER:
                res = self.port.read(2)
                #print('result: ' + str(res))
                # maybe I need to add a delay to solve the problem
                time.sleep(0.001)
                response = res [0]
                num = int.from_bytes(res[1:2], "big")
                if(num != 0):
                    dat_buf = bytes(self.port.read(1))
                    for i in range(num - 1):
                        dat_buf = dat_buf + bytes(self.port.read(1))
                checksum = self.port.read(1)
        result = BEGIN_DELIMITER + bytes(res) + bytes(dat_buf)
        length = 3 + num
        return result, response, length

    def read_distance_buffer(self):
        # print(self.distancebuffer)
        return self.distancebuffer

    
    #   Writings

    def send_message_no_data(self, command):
        self.port.write(BEGIN_DELIMITER + command)

    def send_message_data(self, command, data):
        self.port.write(BEGIN_DELIMITER + command + b'\x01' + data.to_bytes(1, 'big'))

    
    #   Time

    def current_millis_time(self):
        return round(time.time() * 1000)


    #   Task

    def task(self):

        # prev_time = self.current_millis_time()
        
        while 1:

            #   Polling positions each second ***1***
            # curr_time = self.current_millis_time()
            # if(curr_time > prev_time + 1000):
            #     self.get_positions()
            #     prev_time = curr_time


            #   Read all incoming messages

            result, respons, length = self.read_respons()
            if(respons != 0):

                # -- DEBUG --
                #   print('Resp: ' + str(respons))
                #   print(result)
                #   print(str(int.from_bytes(AUTO_POS_IND, "big")) + ' =? ' + str(respons)) 
                
                #   Currently IN USE
                if(respons == int.from_bytes(AUTO_POS_IND, "big")):
                    for i in range(12):
                        self.distancebuffer [i] = int.from_bytes(result[3+i:4+i], "big")
                
                #   Currently not used -- by polling each second 'get_positions' ***1***
                if(respons == int.from_bytes(POSITIONS_ALL_RSP, "big")):
                    for i in range(12):
                        self.distancebuffer [i] = int.from_bytes(result[3+i:4+i], "big")

                #   Currently not used
                if(respons == int.from_bytes(ALERT_IND, "big")):
                    a = 1
                    # Do something with the alert indication

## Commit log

2023-02-15 update clean-up
    [Assembly.SLDASM, Assembly_V2.SLDASM, LEDSTRIP_Mounting.STL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]
2023-03-20 Add encoder motor files

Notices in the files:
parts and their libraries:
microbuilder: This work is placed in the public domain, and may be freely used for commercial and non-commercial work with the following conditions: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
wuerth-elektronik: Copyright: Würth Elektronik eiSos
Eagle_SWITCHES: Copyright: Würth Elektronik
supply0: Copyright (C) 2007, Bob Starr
